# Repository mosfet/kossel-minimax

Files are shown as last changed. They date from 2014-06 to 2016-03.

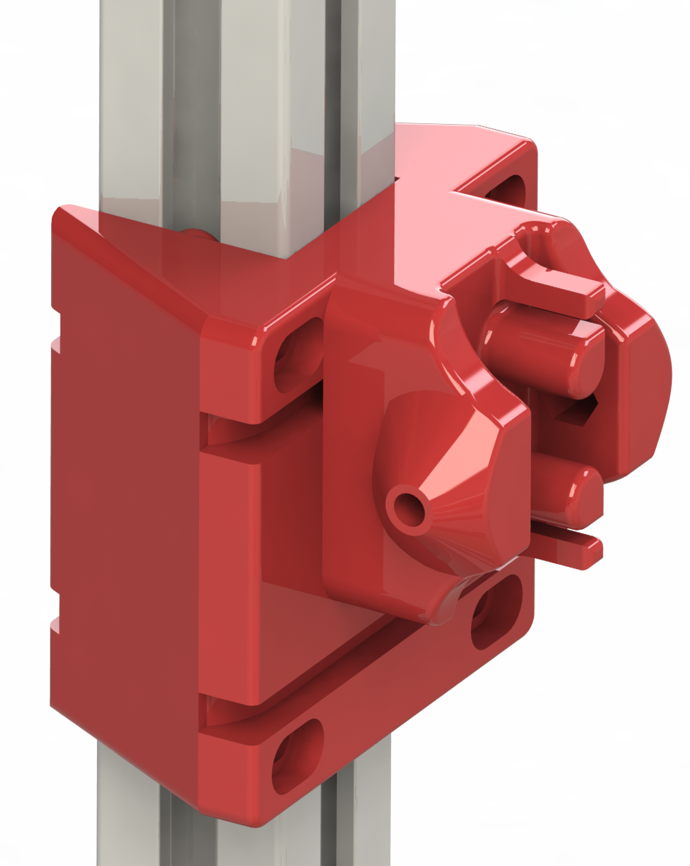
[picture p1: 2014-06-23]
preview/preview-printed-bushing.PNG

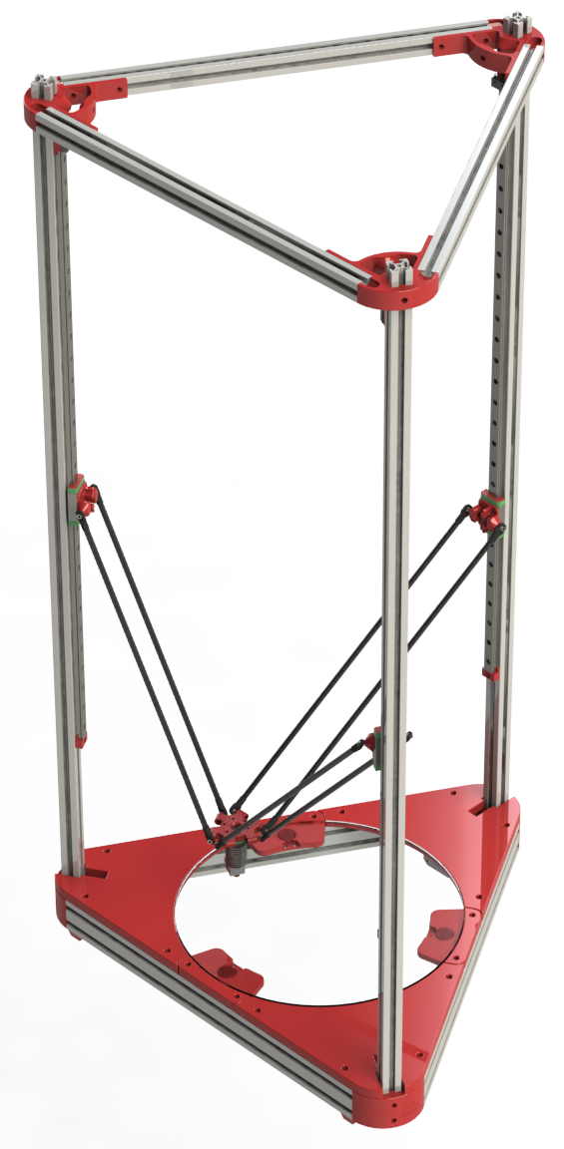
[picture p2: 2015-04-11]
preview/preview-overview.png

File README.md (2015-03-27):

###Kossel Minimax

Based on Johan's Kossel Mini @ github.com/jcrocholl/kossel/

Completely remodeled in Solidworks for Misumi 2020 and 2040 extrusions and a much bigger print area (300mm diameter print plate, ~470mm cylindrical print height, ~500mm tower print height, 1000mm overall height)

**Basic BOM:**

For belts, thid design uses 2020mm GT2 belts for each axis, 6060mm total, get a bit more to be safe.

* Aluminum Extrusion 2020 (length 420mm qty3 and length 1000mm qty3) (http://us.misumi-ec.com/vona2/detail/110302368740/ Choose Carefully!)
* Aluminum Extrusion 2040 (length 420mm qty3)  (http://us.misumi-ec.com/vona2/detail/110302368830/ - Choose Carefully!)
* Bag of extrusion nuts (qty1) HNKK5-3 (http://us.misumi-ec.com/vona2/detail/110302246940/)
* 300mm diameter round glass plate (such as http://www.amazon.com/Clear-Borosilicate-Glass-Printers-Round/dp/B00GRHFIC0)

Kossel Mini fasteners BOM, bearings BOM, 3x Nema  17 motors for motion, bowden extruder of your choice with enough bowden tube

**The design has 3 different types of vertical movement types available:**

1. *Steel Linear bearing:* MGN 12H rails and bearing cartridges, 600mm (like http://www.ebay.com/itm/161304571537)
  - Pros: superior rigidity, longevity, and backlash tolerances. Not a lot of material to print. 
  - Cons: expensive (over 150$USD for three 800mm long rails with bearings)
 
2. *Printed linear bearing:* Uses 5/16th delrin balls found on amazon (http://www.amazon.com/gp/product/B000FMWFXI/ 2 packs). 
  - Pros: Bearings are cheap, about $10 for plenty of balls, decent longevity, nearly fully 3d printed solution
  - Cons: Can be noisy, and requires a good printer to make bearings with smooth channels to facilitate smooth travel. 
	
3. *Printed linear bushings:* PLA bushings that slide over the extrusions.
  - Pros: Fully 3d-printed solution, lightweight solution, can be assembled and tightened with zip-ties
  - Cons: May wear over time requiring replacement or tightening to eliminate backlash and wobble.

Kossel mini assembly instructions apply, with a slight difference on the upper vertex:

  There is an embedded nut trap on the inside of the bearing area. On top of that is a single washer followed by the two flanged bearings, and then another washer.
  
  The tensioner could use a larger washer than the Kossel mini's instruction, or perhaps some printed solution. I use an additional set of m4 washers under the m3 washers.

*TODO:*

Design effector plate, extruder fan shroud, auto level probe mount.
  
  You can use regular Kossel mini parts for these if you want to print it now.

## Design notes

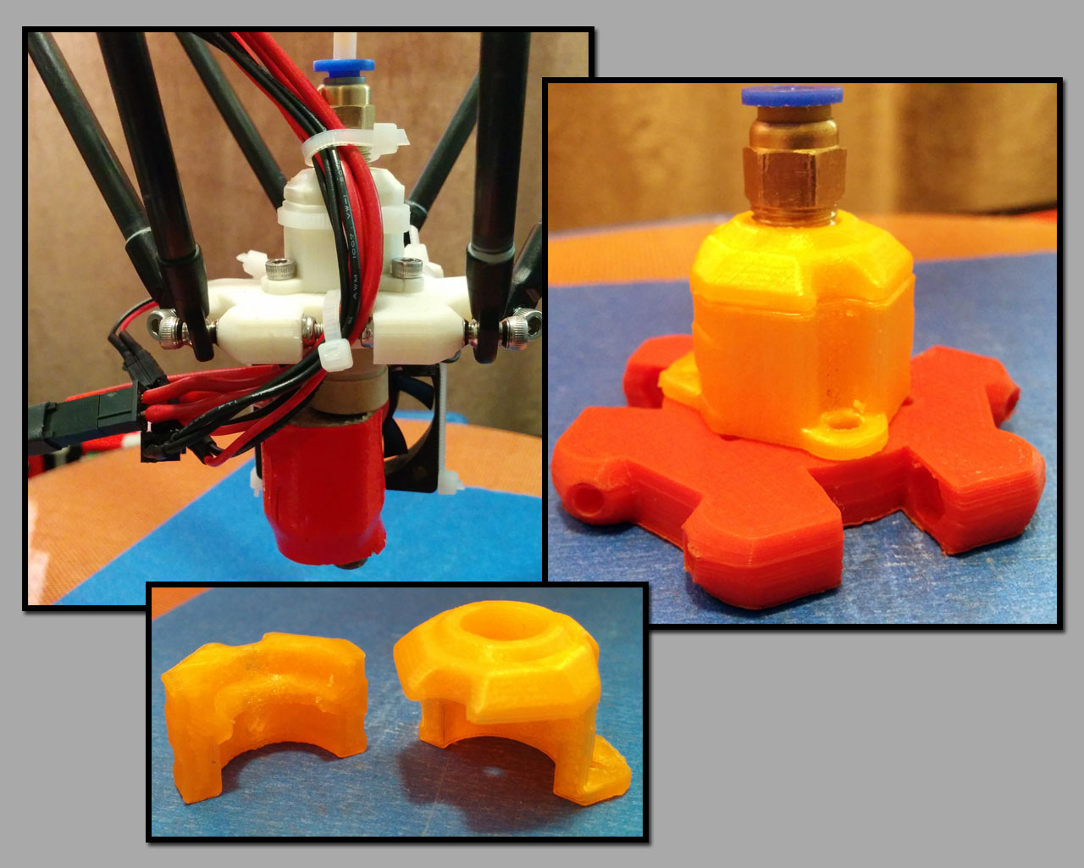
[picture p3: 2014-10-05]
photos/ubis.jpg

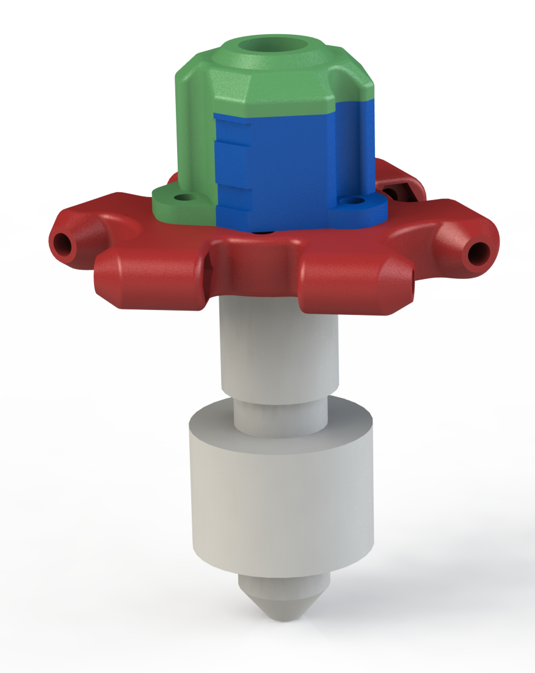
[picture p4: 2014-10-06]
preview/preview-effector-ubis.png

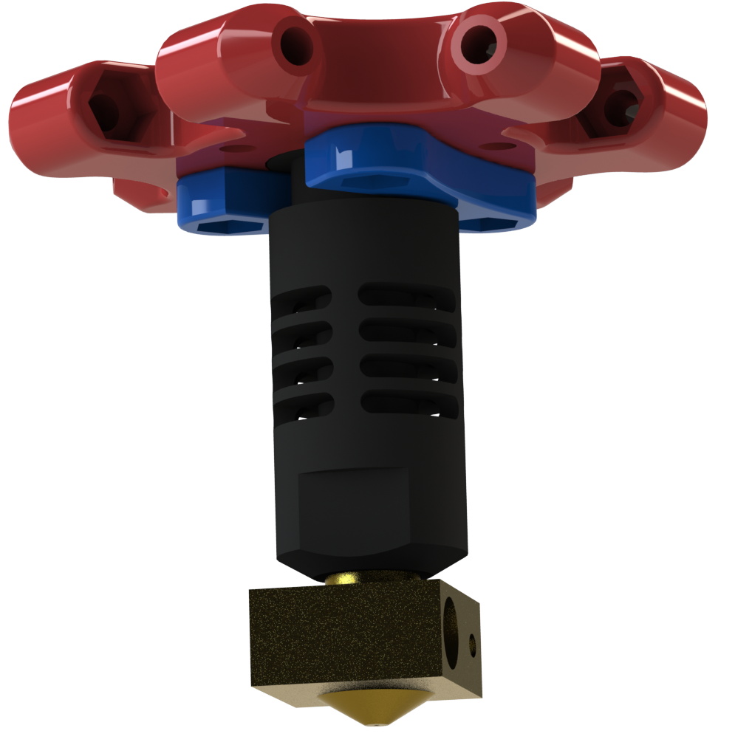
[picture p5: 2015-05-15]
preview/preview-effector-jhead.png

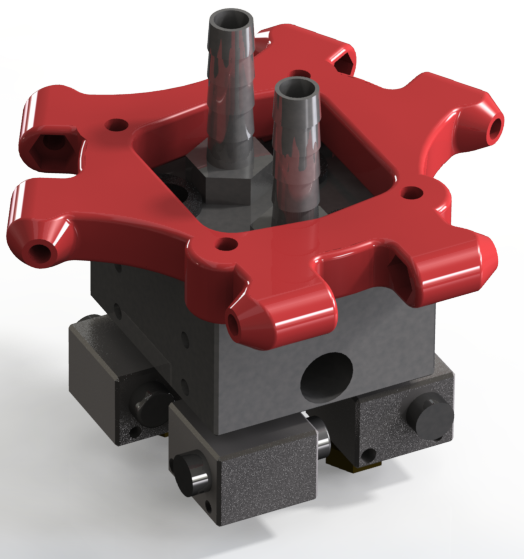
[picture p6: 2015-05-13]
preview/preview-effector-kraken.png

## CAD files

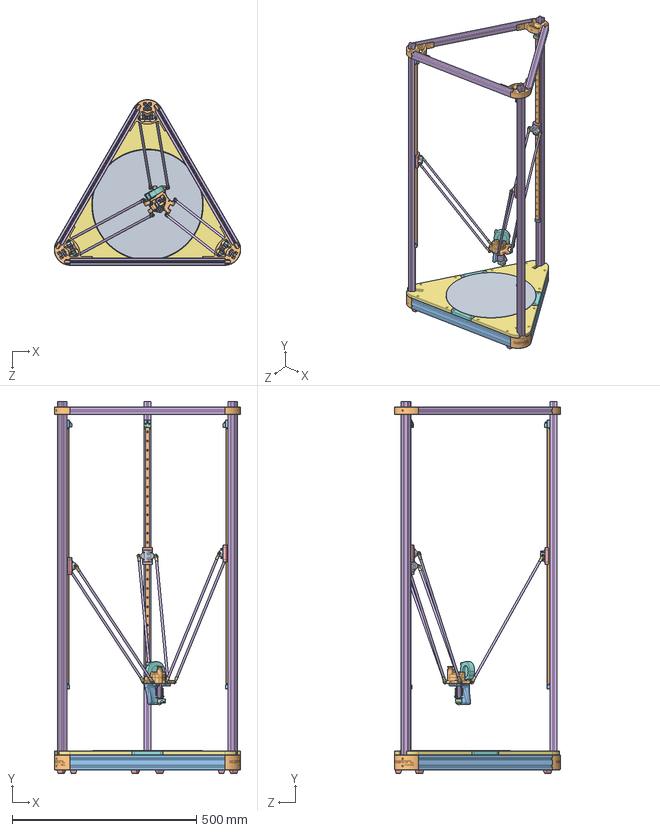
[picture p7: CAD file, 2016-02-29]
assembled_complete.SLDASM
506.2 x 1010.0 x 449.9 mm
glass_plate_300mm
vertex x 6
misumi-HFSB5-2040-extrusion x 3
nema_17_steppermotor x 3
foot x 6
misumi-HFSB5-2020-extrusion x 6
motor_cover x 3
bedrest-fsr x 3
bedrest-fsr-foot x 3
mgn12h_linear_rail x 3
stop x 6
ss-56L_switch x 3
mgn12h_linear_rail_cartridge x 3
rod_6mm4mm x 6
connector^Traxxas_5347 x 12
ball^Traxxas_5347 x 12
rod_and_belt_carriage x 3
effector x 2
effector_clip
block^hotend-e3d-v6
break^hotend-e3d-v6
sink^hotend-e3d-v6
nozzle^hotend-e3d-v6
flex3drive-gear-mockup

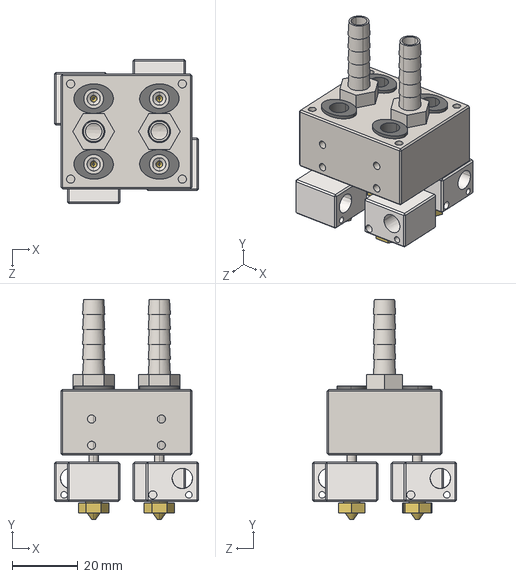
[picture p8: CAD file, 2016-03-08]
iges/assembled_kraken.igs
44.0 x 67.0 x 44.0 mm

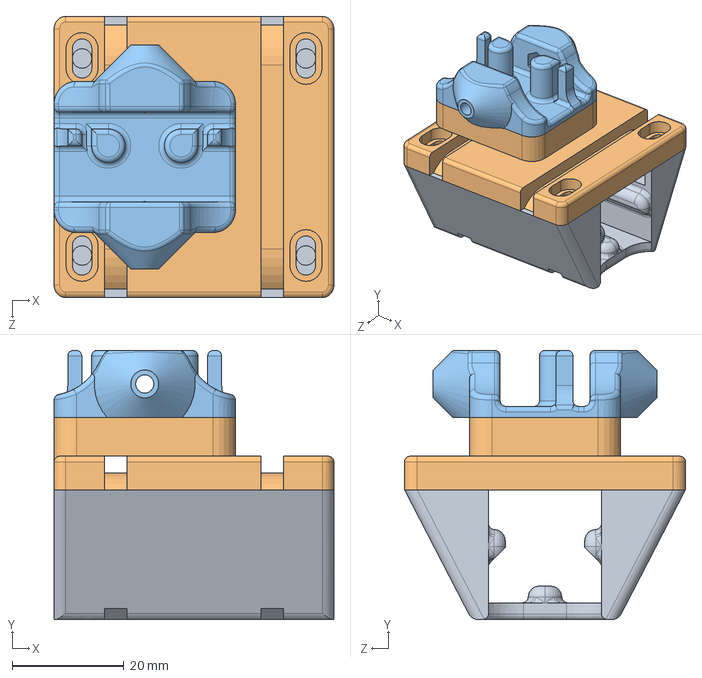
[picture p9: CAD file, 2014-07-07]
option-printed-bushing/assembled_bushing.SLDASM
50.0 x 48.1 x 50.2 mm
bushing_cover
rod_and_belt_carriage

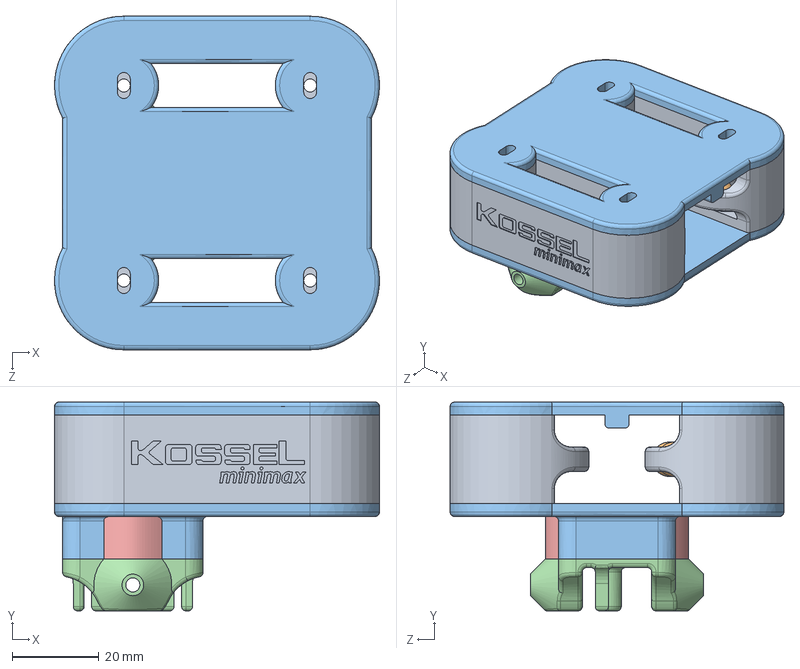
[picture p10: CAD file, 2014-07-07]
option-printed-bearing/assembled_bearing.SLDASM
75.0 x 48.2 x 77.0 mm
bearing_body x 2
delrin_ball_5-16_inch x 19
bearing_assembly_plate x 2
rod_and_belt_carriage
Part2^assembled_bearing

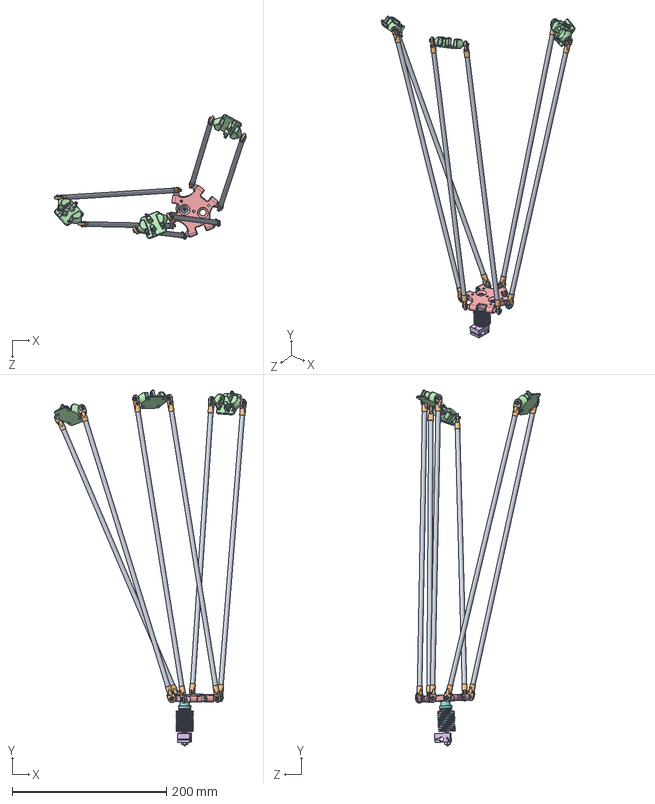
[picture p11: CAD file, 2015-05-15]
assembled_spider.SLDASM
249.2 x 461.4 x 161.7 mm
rod_6mm4mm x 6
connector^Traxxas_5347 x 12
ball^Traxxas_5347 x 12
rod_and_belt_carriage x 3
effector
block^E3D V6 1.75 Uni model
break^E3D V6 1.75 Uni model
sink^E3D V6 1.75 Uni model
nozzle^E3D V6 1.75 Uni model

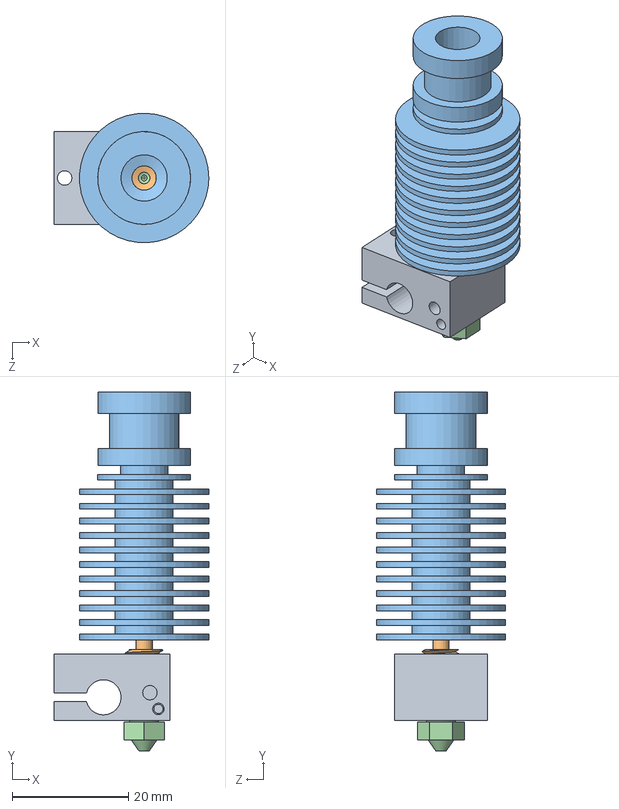
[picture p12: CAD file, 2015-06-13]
nonprinted_reference_parts/E3D V6 1.75 Uni model.SLDASM
26.6 x 61.9 x 22.3 mm
block^E3D V6 1.75 Uni model
break^E3D V6 1.75 Uni model
sink^E3D V6 1.75 Uni model
nozzle^E3D V6 1.75 Uni model

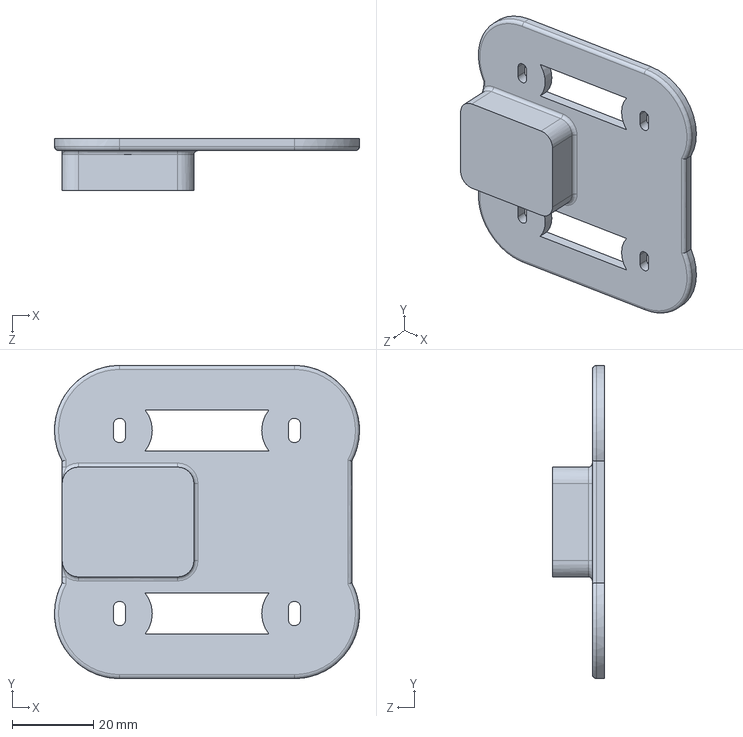
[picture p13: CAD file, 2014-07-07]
option-printed-bearing/bearing_assembly_plate.sldprt
75.0 x 77.0 x 12.8 mm

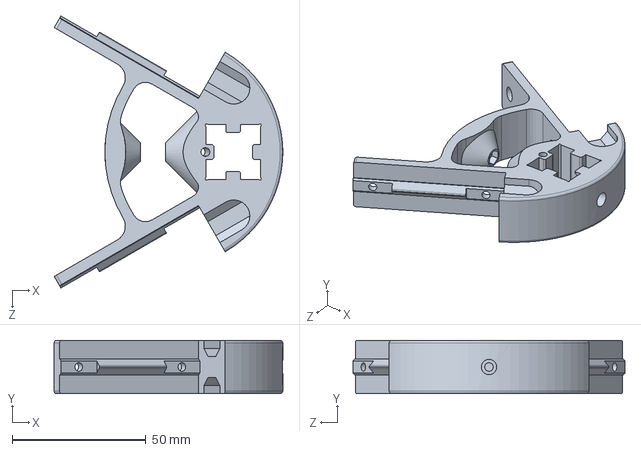
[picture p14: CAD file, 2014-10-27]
assembled_lower_upper_frame.SLDASM
85.5 x 20.0 x 101.7 mm

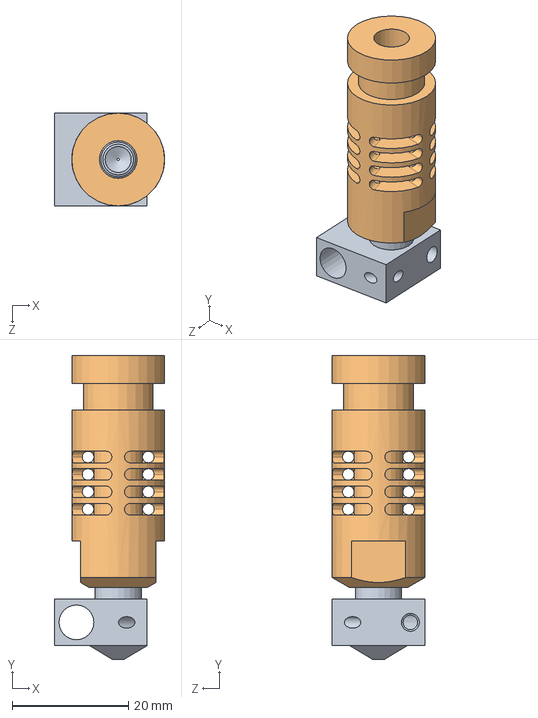
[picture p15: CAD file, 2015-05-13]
nonprinted_reference_parts/JHead_Nozzle.SLDASM
19.0 x 52.4 x 16.0 mm
Part1^JHead_Nozzle
Part2^JHead_Nozzle

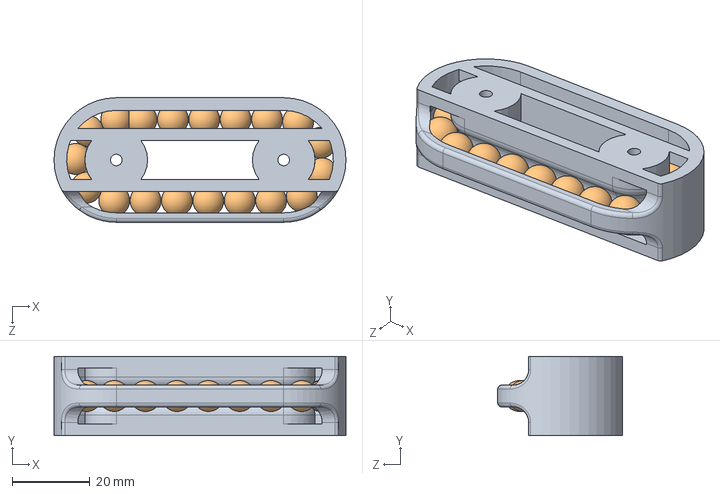
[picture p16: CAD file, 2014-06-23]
option-printed-bearing/loaded_bearing_body.SLDASM
75.0 x 20.4 x 32.0 mm
bearing_body
delrin_ball_5-16_inch x 19

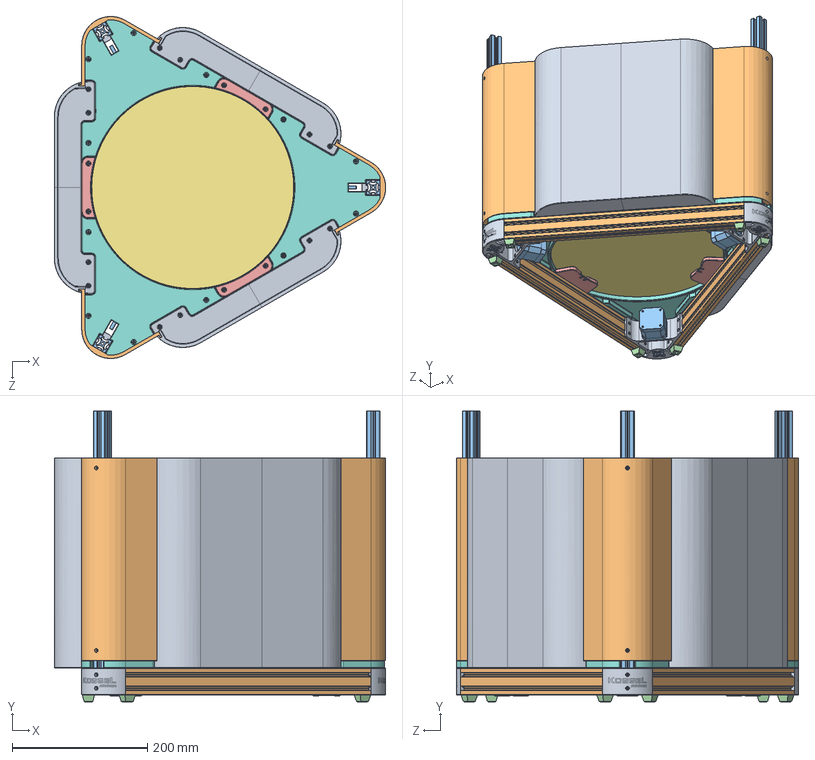
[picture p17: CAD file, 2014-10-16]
assembled_enclosure.SLDASM
490.4 x 430.0 x 506.2 mm
vertex x 3
misumi-HFSB5-2040-extrusion x 3
nema_17_steppermotor x 3
foot x 6
bedrest-fsr x 3
bedrest-fsr-foot x 3
glass_plate_300mm
motor_cover x 3
enclosure_base x 3
enclosure-backwall x 3
misumi-HFSB5-2020-extrusion x 3

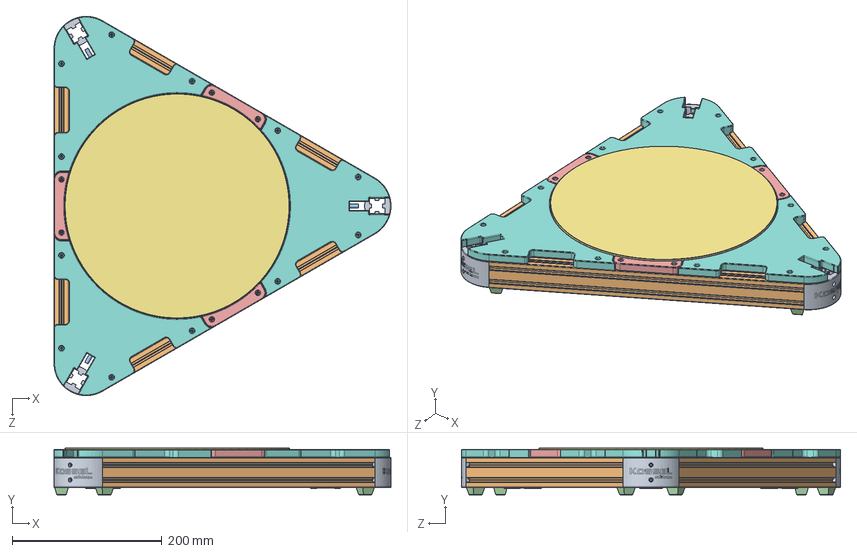
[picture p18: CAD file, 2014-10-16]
assembled_motor_covers.SLDASM
449.9 x 62.6 x 506.2 mm
vertex x 3
misumi-HFSB5-2040-extrusion x 3
nema_17_steppermotor x 3
foot x 6
bedrest-fsr x 3
bedrest-fsr-foot x 3
glass_plate_300mm
motor_cover x 3

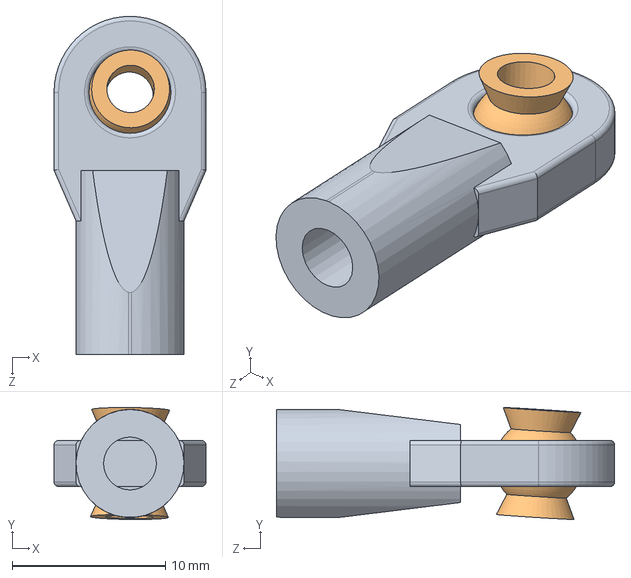
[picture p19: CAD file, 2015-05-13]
nonprinted_reference_parts/Traxxas_5347.SLDASM
9.91 x 7.30 x 22.0 mm
connector^Traxxas_5347
ball^Traxxas_5347

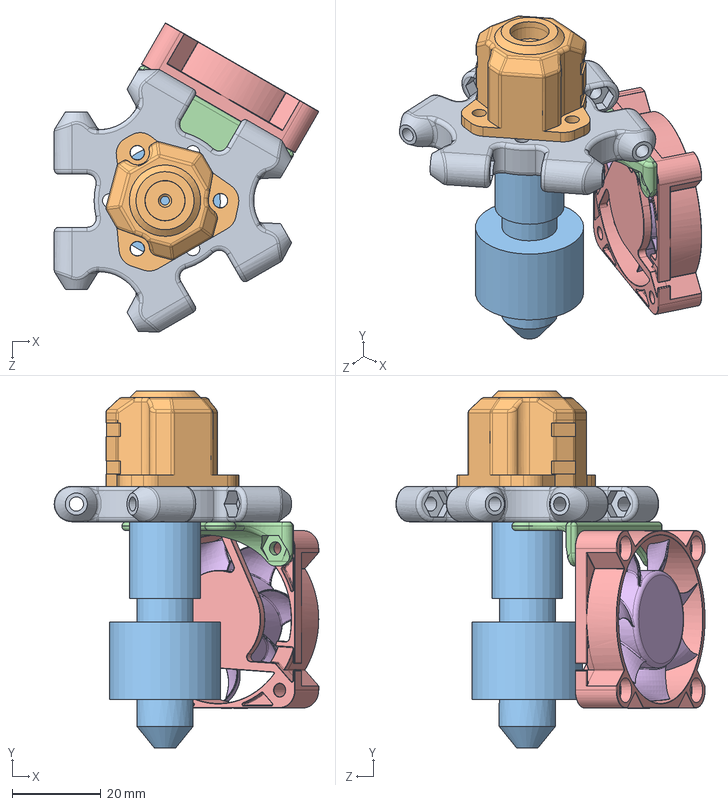
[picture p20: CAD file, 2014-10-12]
assembled_hotend_ubis.SLDASM
59.7 x 80.5 x 69.7 mm
effector
ubis_holder x 2
ubis hotend
effector_fan_40mm
body^40mm-fan
blades^40mm-fan

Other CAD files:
nonprinted_reference_parts/e3d-kraken/assembled_kraken.SLDASM
assembled_effector.SLDASM
nonprinted_reference_parts/hotend-e3d-v6.SLDASM
assembled_extruder_dd.SLDASM
STEP/50x15_blower_fan_20mm_opening.step
STEP/E3D Heat Block.step
STEP/E3D Nozzle.step
STEP/E3D V6 1.75 Uni model.step
STEP/JHead_Nozzle.step
STEP/Kraken Compression Coupling.step
STEP/Kraken Cooling Block.step
STEP/Kraken Heat Break.step
STEP/Traxxas_5347.step
STEP/assembled_bearing.step
STEP/assembled_bedrest-fsr.step
STEP/assembled_bushing.step
STEP/assembled_extruder_hobbed.step
STEP/assembled_hotend_e3dv6.step
STEP/assembled_rod.step
STEP/assembled_stops.step
STEP/bearing_16x5.step
STEP/bearing_22x7.step
STEP/bearing_assembly_plate.step
STEP/bearing_body.step
STEP/bed-rest.step
STEP/bedrest-fsr-foot.step
STEP/bedrest-fsr.step
STEP/bowden_tube.step
STEP/bracing_build.step
STEP/bushing_body.step
STEP/bushing_cover.step
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

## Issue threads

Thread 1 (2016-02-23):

Bearings and Files

mgiaco, 2016-02-23:
Hello do I need 600mm linear bearings for this printer or 800mm? I can't open the files.  Is it possible to convert the files to step?

Thanks Mathias

mgiaco, 2016-02-23:
Second question is it possible that you upload some detailed pictures,  I want to build that printer it looks very nice.  Thanks

mosfet, 2016-02-23:
I use 800mm linear rails because I have 1000mm long vertical extrusions, and they work fine but are a bit long. If I were building it again, I would actually shorten both the vertical extrusion length to 800mm and use 600mm rails - I have yet to use anywhere near the full print height, and I'm not sure the increase in price is worth it, for me.

I'm sure you've seen all the pics from https://github.com/mosfet/kossel-minimax/tree/master/preview but there are a few more posted here, of a couple different builds: https://imgur.com/a/vriql#0

mgiaco, 2016-02-29:
Thanks for your help. Is it possible that you save the Solidworks Assembled File in a Step or IGES format. So I can open it without Solidworks for assembling.

thanks
kind regards,
Mathias

mosfet, 2016-02-29:
I generally keep them in SW format since they have multiple configurations
(motor covers with and without room for enclosure clamps, extra pieces from
here and there) and parameters (i.e. can adjust the size of things and
everything else also automatically adjusts).

However, I did export all the files to STEP files and uploaded them to the
STEP folder. Hopefully they'll include all configuration data and can be
adjusted easily if you need to.

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

mgiaco, 2016-03-01:
Thanks, it works fine. But the assembled parts are missing :-( so i searched for some other tools today. Now I found the eDrawings Tools on the Solidworks Website today. And the great thing is that this viewer could be used for free. But it seems that some of the assembled files aren´t up to date. The file assembled_extruder_dd.SLDASM as an example could not be opened with this viewer something seems to be not up to date. It would be great if you can fix that but the main file assembled complete works fine no I can build it if i get the printed parts.

Really really big thanks for your support and for your awesome work. Thanks for sharing it.

best regards from austria,
Mathias

mgiaco, 2016-03-07:
Hello,

Sorry that I ask you again. Is it possible that you do a refresh on the Solidworks Files? I cannot update the Files with the viewer only. But there seems to be something wrong so I cannot open some assembled files. Is it possible that you save the assembled as step or iges also?

thanks a lot.
best regards

mosfet, 2016-03-09:
I reposted all the converted files in both STEP and IGES format, including the assemblies, so you should have everything.

mgiaco, 2016-03-09:
You are really awesome.
many many thanks for that commit
Mathias

Closed 2016-03-14.

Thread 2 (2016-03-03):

Recommended stepper motor

mgiaco, 2016-03-03:
Hello,

Should I go with a default Nema 17 also used on the Kossel mini?

thanks
Mathias

mosfet, 2016-03-03:
Yep, no problem, the amount of mass that is moved is minimal, and its
shared evenly across all motors. The 1.2A or 1.7A motors normally used on a
reprap should be fine.

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

mgiaco, 2016-03-03:
Thanks that's sounds great.

Closed 2016-03-03.

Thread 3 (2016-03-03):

Carbon-rods?

mgiaco, 2016-03-03:
What kind of carbon rods are you using? The only rods I found are:
http://builda3dprinter.eu/product/carbon-rods-kossel-xl/

thanks

mosfet, 2016-03-03:
I bought from ebay, search for "6mm OD x 4mm Carbon fiber tube" if you're
using the traxas connectors used in the kossel mini.

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

mgiaco, 2016-03-03:
Okay thanks and what about the length I measured 360mm from the CAD.

mosfet, 2016-03-03:
Yep, I cut mine with a dremel. The length doesn't need to be perfectly
360.22mm long (you'll calibrate that later), but it is important that all
rods are the same length. There is a few guides around that can help
facilitate this, but for me, I strapped the dremel tool with a cutoff blade
to a length of wood, and drilled a small wood endstop about 360mm away from
the cutting blade and trimmed all the rods this way.

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

mgiaco, 2016-03-03:
Okay really thanks for your fast support.
mathias

Closed 2016-03-03.

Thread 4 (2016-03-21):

Extruder

mgiaco, 2016-03-21:
Hello Mosfet,

Do you have any real life picture from the Extruder? We want to build the E3d dual head option. And we are not sure what kind of extruder we should use from your files.

thanks
mathias

mosfet, 2016-03-21:
I actually never tested the extruder files, I've always used a wades
extruder with a bowden extension. I've bolted the wades up to the extrusion
using the part wade_mount.

See https://i.imgur.com/KCTG07P.jpg and https://i.imgur.com/Tup3OXS.jpg.

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

mosfet, 2016-03-21:
Hmm, unless you're referring to the effector, as there is an effector assembly, but uses multiple configurations in order to switch between effector modes.

I'm not sure if this data was included in the STEP / IGES files, but i can export a particular configuration if need be.

mosfet, 2016-03-21:
I've uploaded IGES and STEP files for effector_dual_e3d and effector_clip_dual_e3d.

mgiaco, 2016-03-21:
Thanks

Closed 2016-04-05.

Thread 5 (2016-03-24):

Print Plate

mgiaco, 2016-03-24:
Hello,
Do you have some information about your print plate?
Can you give me some information about the layer structure?
What power has your heating foil?

Thanks.

mgiaco, 2016-04-05:
So I found the information on your photos - sorry for the duplicated question. Do you have no problems with the temperature concerning the MDF plate?

Closed 2017-09-06.

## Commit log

2014-06-23 initial commit
    kossel minimax initial commit
    [assembled_bearing.SLDASM, assembled_bushing.SLDASM, assembled_complete.SLDASM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]
2014-06-23 add rod length calucations to main assembly
    [assembled_complete.SLDASM, assembled_vertex.SLDASM]
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2014-06-24 add endstop and ready to slice files
    [assembled_complete.SLDASM, assembled_endstop.SLDASM, assembled_vertex.SLDASM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]
2014-06-24 make vertex stabilizging bumps more printable
    45 degree fillets instead of round chamfers
    [vertex-upper.STL, vertex.SLDPRT]
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2014-07-05 add wade mount, carriage stop, better endstop
    [assembled_complete.SLDASM, assembled_endstop.SLDASM, assembled_vertex.SLDASM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]
2014-07-05 wade mount preview and update
    [wade_mount.SLDPRT]
2014-07-06 update to wade mount, add traxxas collet
    Wade mount moves the motor away from the vertical extrusion, in case the
    bowden cable screws with the carriage goin up n down.
    traxxas collet is used to center a traxxas end in a chuck for even
    tapping.
    [traxxas_collet.SLDPRT, traxxas_collet.STL, wade_mount.SLDPRT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]
2014-07-07 update to traxxas collet and wade mount
    [assembled_complete.SLDASM, traxxas_collet.SLDPRT, traxxas_collet.STL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]
2014-07-07 generate STL for the printed bearing and printed bushing
    [assembled_bearing.SLDASM, assembled_bushing.SLDASM, bearing_assembly_plate.sldprt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]
2014-07-09 add kossr mount for 2040, melzi holder
    [kossr_mount.SLDPRT, kossr_mount.STL, melzi_holder.SLDPRT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]
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2014-07-13 extruder cooling fan & print cooling fan
    for jhead / groovemount
    [assembled_hotend.SLDASM, hotend-cooling-fan.SLDPRT, hotend-cooling-fan.STL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]
2014-07-20 add upper & lower stabilizers
    for those who want to add more vertical extusions for stability, or to
    mount the extruder
    [stabilizer_extrusion_block.SLDPRT]
2014-07-27 make hotend fans harder better faster stronger
    [assembled_hotend.SLDASM, hotend-cooling-fan.STL, hotend-extruder-fan.STL]
2014-07-27 bed rest for force sense resistors
    [bed-rest-fsr-foot-hi-sensitivity.STL, bed-rest-fsr-foot-low-sensitivity.STL, bed-rest-fsr-foot-med-sensitivity.STL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]
2014-07-29 rotate fsr parts for printing
    [bed-rest-fsr-foot-hi-sensitivity.STL, bed-rest-fsr-foot-low-sensitivity.STL, bed-rest-fsr-foot-med-sensitivity.STL]
2014-07-31 update bed rest and parts with actual dimensions
    [assembled_bedrest-fsr.SLDASM, bed-rest-fsr-foot-hi-sensitivity.STL, bed-rest-fsr-foot-low-sensitivity.STL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]
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2014-09-19 add plated stl files for printing on printrbot
    150x150 mm or 6x6 inch print area req'd
    [1x-bedrests.stl, 3x-tower-plate.stl, effector-from-kosselmini.stl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]
2014-09-27 added electronics enclosure draft
    [electronics_enclosure.SLDPRT, electronics_enclosure.STL]
2014-09-27 rotate and fix normals
    [electronics_enclosure.STL]
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2014-09-27 update add usb hole and adjust the way the cables come in
    [electronics_enclosure.SLDPRT, electronics_enclosure.STL]
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2014-09-28 add jhead fans and update electronics enclosure
    [electronics_enclosure.SLDPRT, electronics_enclosure.STL, jhead geetech.SLDPRT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]
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2014-10-02 add ubis holder stl
    [ubis_holder.STL]
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2014-10-02 add effector modified for ubis hotend
    [effector-from-kosselmini-ubis.stl]
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2014-10-04 better update to dd extruder
    [extruder_dd_body.STL]
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2014-10-05 add parts for ubis hotend
    ubis ftw!
    [ubis-effector.stl, ubis_holder.SLDPRT, ubis_holder.STL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]
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2014-10-05 add dd parametric extruder
    also update fan stls
    [extruder_dd_body.sldprt, jhead-fans-lock.STL, jhead-fans-print.STL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]
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2014-10-06 add effector to assemblies
    [assembled_hotend.SLDASM, assembled_hotend_groovemount.SLDASM, assembled_hotend_jhead.SLDASM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]
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2014-10-07 update e3d effector graphic & groovemount clip
    [E3D V6 1.75 Uni model.SLDASM, groovemount_clip_e3d.SLDPRT]
2014-10-08 much updates. many 3d. wow.
    [50x15_blower_fan_20mm_opening.SLDPRT, assembled_hotend_e3dv6.SLDASM, assembled_hotend_jhead.SLDASM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]
2014-10-09 add assembled extruder
    other updates too
    [50x15_blower_fan_20mm_opening.SLDPRT, assembled_extruder_dd.SLDASM, assembled_hotend_ubis.SLDASM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]
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2014-10-10 moar pretty, add chamfer to the worm gear
    [metal gear.SLDPRT]
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2014-10-12 updates to overall view..
    lots of reference adds
    [Traxxas_5347.SLDASM, assembled_complete_redux.SLDASM, assembled_hotend_ubis.SLDASM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]
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2014-10-15 add motor covers
    keeps crap out from under the bed
    [assembled_complete.SLDASM, assembled_lower_upper_frame.SLDASM, assembled_motor_covers.SLDASM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]
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2014-10-16 add stabilizing bar to fit in the extrusion
    [enclosure-backwall.sldprt]
2014-10-18 add extruder for hobbed bolts from wades.
    this has a particular mount for the inside of a wooden enclosure. A
    bowden tube is used to feed filament into the extruder.
    [assembled_extruder_hobbed.SLDASM, bearing_22x7.SLDPRT, bowden_tube.SLDPRT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]
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2015-04-11 update preview files, add flex effector
    [assembled_effector_flex3drive.SLDASM, effector_flex3drive.SLDPRT, effector_flex3drive.STL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]
2015-04-11 rotate stl flex effector for printing
    [effector_flex3drive.STL]
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2015-05-10 fix dumb extrusion direction error with print support material
    [effector_dual_bowden.SLDPRT, effector_dual_bowden.STL]
2015-05-13 fix error that felix found
    [Traxxas_5347.SLDASM, assembled_complete.SLDASM, assembled_effector_flex3drive_custom.SLDASM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]
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2015-05-13 update effector, combine effector models into one file
    [JHead_Nozzle.SLDASM, assembled_effector.SLDASM, assembled_kraken.SLDASM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]
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2015-05-15 add flex drive to effector config
    [assembled_complete.SLDASM, assembled_effector.SLDASM, assembled_spider.SLDASM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]
2015-05-15 add stl for flex drive effectors
    [effector_flexdrive_bottom_e3d.STL, effector_flexdrive_bottom_jhead.STL, effector_flexdrive_top.STL]
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2015-06-13 udpate effector with new flex drive + more
    new awesome curved fan duct
    [E3D V6 1.75 Uni model.SLDASM, assembled_complete.SLDASM, assembled_effector.SLDASM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]
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2016-03-21 add e3d dual effector and clip for mathias
    step and iges
    [effector_clip_dual_e3d.IGS, effector_clip_dual_e3d.STEP, effector_dual_e3d.IGS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]
